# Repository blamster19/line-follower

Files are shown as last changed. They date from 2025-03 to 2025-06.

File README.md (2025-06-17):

# line-follower
Line follower for robot competition

## Introduction

This repository holds design and code of a line follower robot built for a racing competition which took place on 2025-06-11T17:00+0100 at the Faculty of Physics of University of Warsaw. The robot competed against five other machines and its score was based on the best time in three rounds. Machine built using contents of this repository won the first place with time 00:00:32,90. 
The team included:

* Jan Gers (captain)
* Tomasz Pniewski
* Magdalena Latała
* Maria Waligórska
* Wojciech Knop

Supervisor: Piotr Kaźmierczak

## Construction

### Hardware
1. **Chassis**  
	The chassis was 3D-printed with PLA on Prusa i3 MK3 from files: `./assets/chassis-model.stl`, `./assets/robot-motor-board.stl` and `./assets/robot-motor-shell.stl`. The motor shells were glued to the main body and motors put in them were later immobilized by boards.
2. **Electronics**  
	This is a list of parts used:
	
	|Part|Count|
	|---|---|
	|N20-BT03 micro 10:1 3000RPM - 12V|2|
	|KTIR0711S on 9x14 mm board with pins|7|
	|Solarbotics RW2i|2|
	|Pico Motor Driver HAT|1|
	|Raspberry Pi Pico H|1|
	|Step-down LM2596|1|
	|SparkFun BOB-13906|1|
	|9 V battery + clip|1|
	|Iduino ST1089|1|
	|Wires|a lot|
		
3. **Wiring**  
	Sensor output was connected through the multiplexer. Multiplexer control was connected to pins `27`,`12`,`13` and its output to analog pin `28`. IR sensor was connected to pin `26`. Motor control was done with pins `16`,`17`,`18`,`19`,`20`,`21` through dedicated ports on the driver HAT. The final construction was not utilizing the IR capability because of time reasons, but it should be functional or otherwise require a few tweaks. Step-down was connected to dedicated ports in the driver HAT and set to 8 V output for stability.
	
3. **Decorations**
	Because the team's name is 'Sigmas' we decided to glue small sigmas at the top of the motor shells. Since the track was getting dirty quickly, we wrapped a pipe cleaner around the sensor tray to act as a brush, which is both elegant and functional. To cover the wires we used synthetic pink feathers. We were quite happy with the avant-garde eclectic style of the robot.
	
### Software

The main loop is done with PD algorithm tweaked to the particular track. The program handles the exception of seeing no line (essential on a track with very sharp turns) by keeping memory of the last position of the line seen by the leftmost or rightmost sensor. Majority voting with this memory buffer decides on the direction of sharp turn which continues until any sensor sees black line again.

The code is hopefully well-documented and self-explanatory. The files which must be put in the Pico memory are `./code/main.py`, `./code/buffer.py`, `./code/motors.py`, `./code/pid.py` and `./code/sensors.py`. All alterations to the PD constants and motor speed shall be done inside `main.py`.

## The competition

This machine won with the best time 00:00:32,90. Below are some multimedia created during the event:

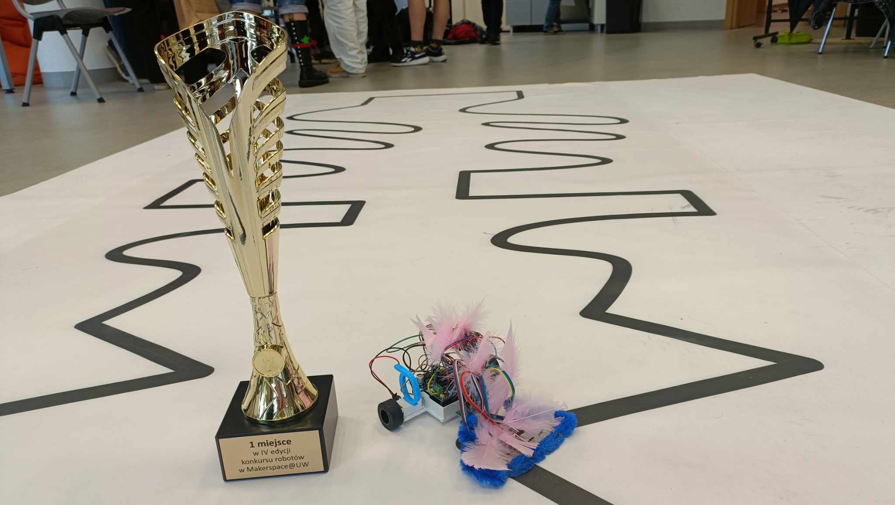
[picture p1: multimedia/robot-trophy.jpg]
Robot standing with the trophy


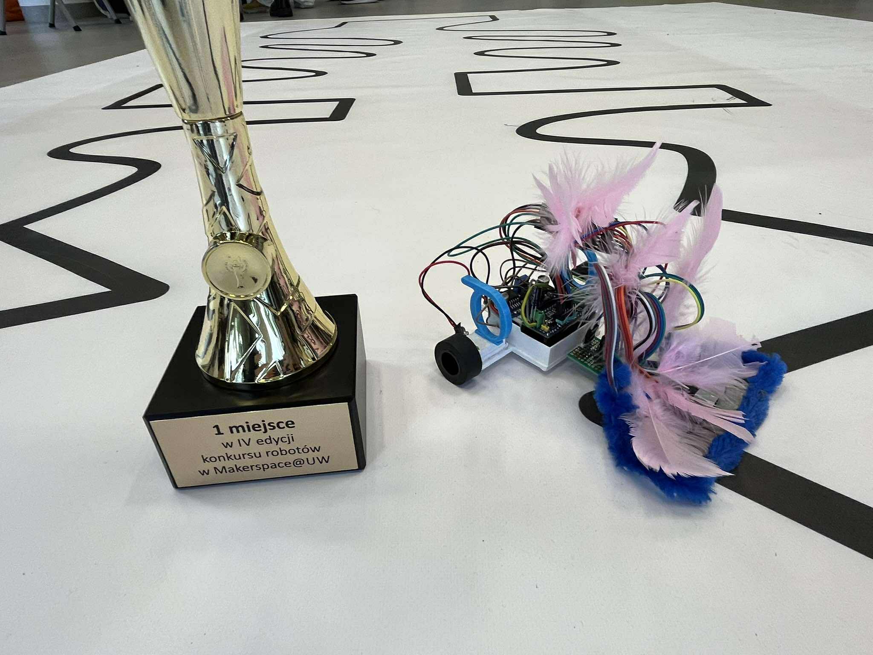
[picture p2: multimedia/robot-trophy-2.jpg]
Robot standing with the trophy closer


Robot following the line

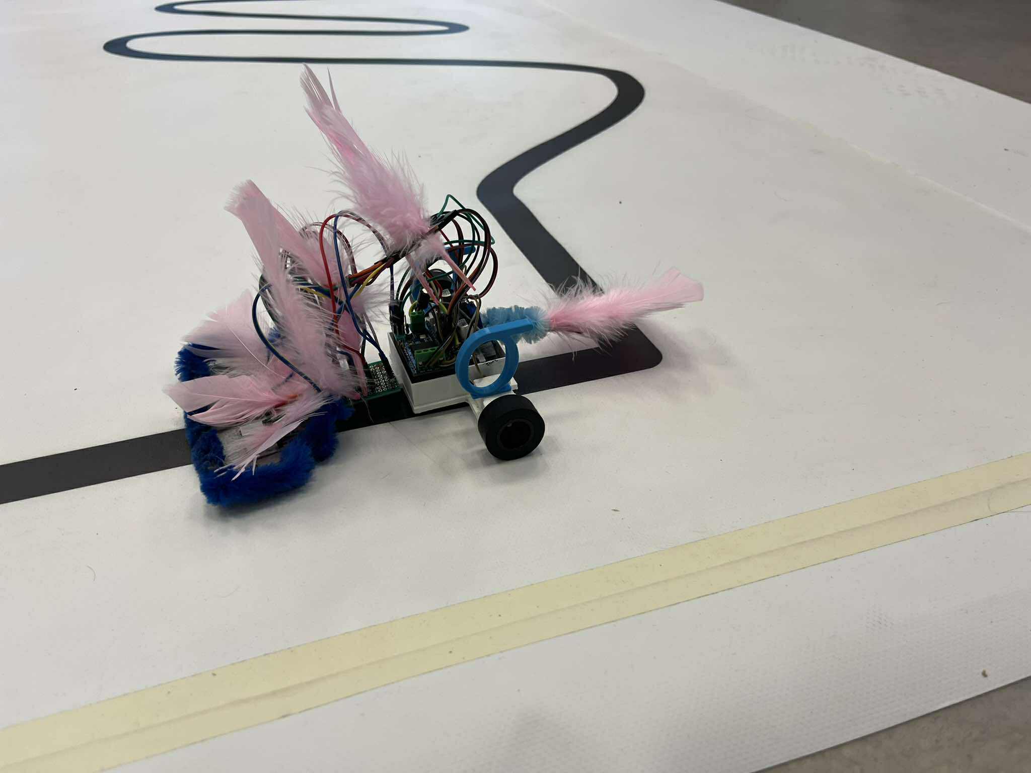
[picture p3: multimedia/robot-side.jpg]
Robot standing on track


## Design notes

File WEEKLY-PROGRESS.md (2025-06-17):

# Weekly progress

## 2025-02-24 -- 2025-03-02

* Arrival of parts: **ok**
* Repository initialization: **ok**
* First draft of chassis model: **ok**
* First print of chassis: **ok**
	* Needs to be better adjusted for printing, too much support needed
	* Relocation of PCBs and battery needed
* Sensor test: **ok**

## 2025-03-03 -- 2025-03-09

* Battery power test: **ok**
* Soldering of motor controller and step-down converter to RPi Pico: **ok**
* Driving test: **failed**
	* Motors pop out of the chassis under the load of battery
	* Motors do not move when weighted down with battery

## 2025-03-10 -- 2025-03-16

* Raising voltage: **failed**
	* Raspberry Pi Pico and potentially motor driver got fried
	* New parts ordered

## 2025-03-17 -- 2025-03-23

* Arrival of parts: **ok**
* Update of chassis model: **ok**
* Print of new chassis: **ok**

## 2025-03-24 -- 2025-03-30

* New motor driver: **ok**
* New power source: **ok**
* Drive test: **ok**
* Analog pin expander: **ok**
* Two-sensor reading: **ok**

## 2025-03-31 -- 2025-04-06

* Sensor calibration preliminary steps

## 2025-04-07 -- 2025-04-13

* Sensor calibration: **partial**
* Sensor code cleanup: **ok**
* Update of chassis model: **ok**
* New parts order: **ok**

## 2025-04-14 -- 2025-04-20

* Print of new chassis: **ok**
* Soldering sensors: **ok**
* Code tweaks: **ok**
* Sharp turn management: **ok**

## 2025-04-21 -- ##2025-04-27

* Soldering sensors: **ok**
* Code tweaks: **ok**
* Fried pin expander: **failed**
	* Pin expander melted the duc tape and stopped working
	* Probably because of prolonged usage

## 2025-04-28 -- 2025-05-04

* May Long Weekend

## 2025-05-05 -- 2025-05-11

* Analog multiplexers ordered instead of expander

## 2025-05-12 -- 2025-05-18

* Multiplexer: **ok**
* Drive test: **ok**
* New sensor code: **ok**

## 2025-05-19 -- 2025-05-25

* Code tweaks: **ok**

## 2025-05-26 -- 2025-06-01

* Installation of voltage converter: **ok**
	* Battery voltage drops caused noticeable speed difference
* New sensor tray: **ok**
* Code tweaks: **ok**
* Installation of two additional sensors: **ok**
* Installation of pipe cleaner in front of sensors: **ok**
* Optical tuning: **ok**
* Robot traverses full path: **partial**

## 2025-06-02 -- 2025-06-08

* New sensor tray: **ok**
* Code tweaks: **ok**
* Robot traverses full path: **success**
* Optical tuning: **ok**

## 2025-06-09 -- 2025-06-15

* Competition finale

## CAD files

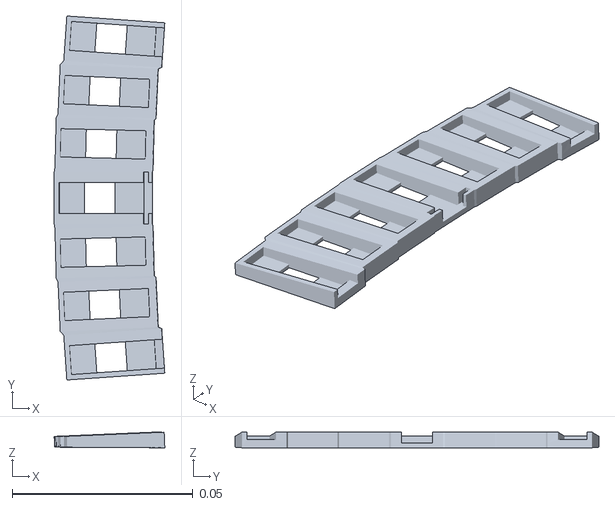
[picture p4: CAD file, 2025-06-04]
assets/sensors_hold.stl
0.0306 x 0.101 x 0.0043

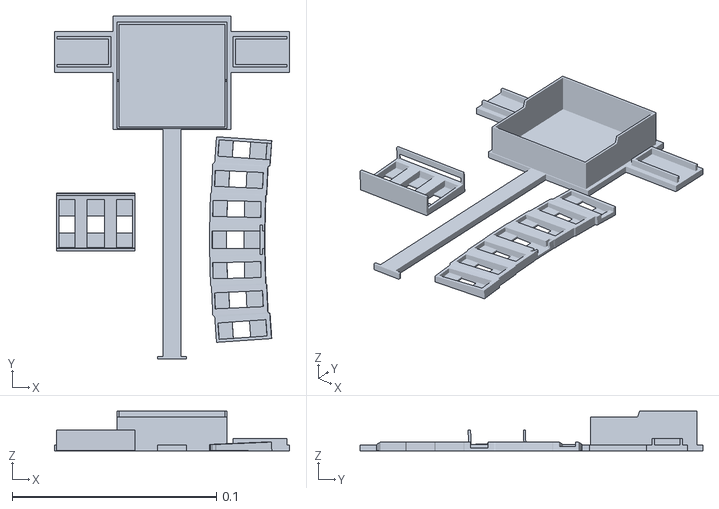
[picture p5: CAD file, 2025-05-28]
assets/chassis-model.stl
0.115 x 0.168 x 0.0195

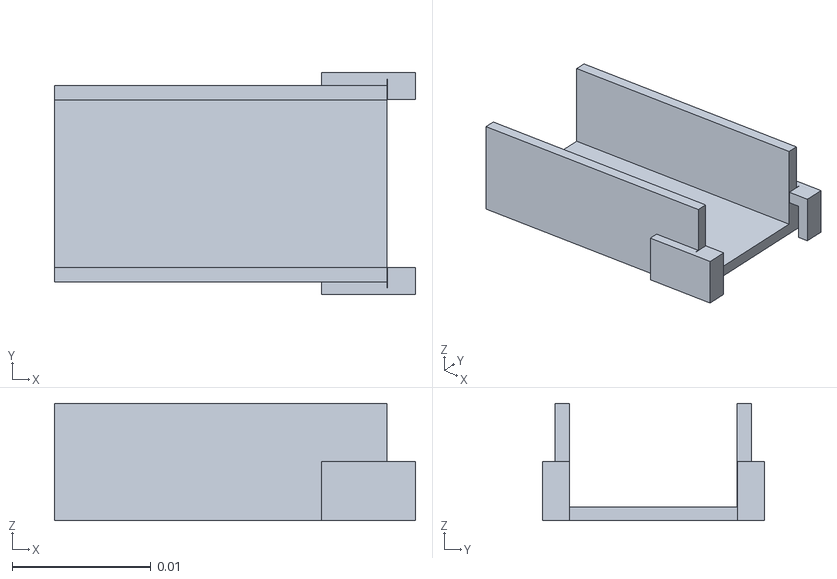
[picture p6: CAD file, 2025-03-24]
assets/robot-motor-shell.stl
0.0261 x 0.016 x 0.00848

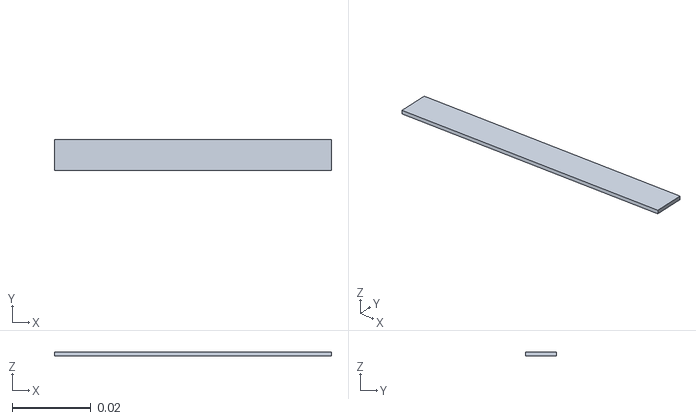
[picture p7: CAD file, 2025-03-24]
assets/robot-sensor-down-board.stl
0.0704 x 0.00781 x 0.000894

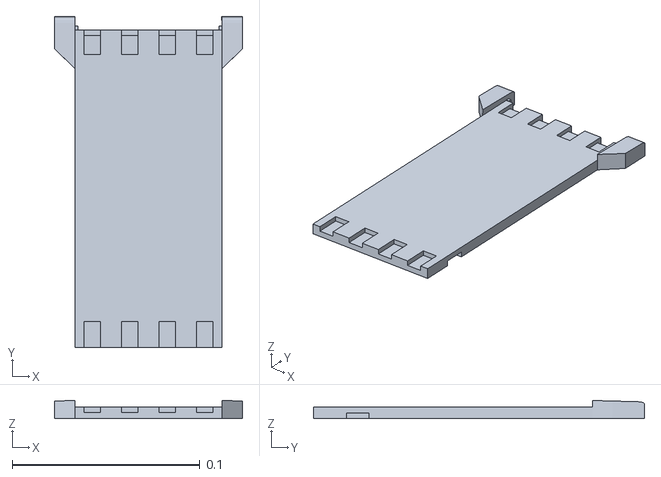
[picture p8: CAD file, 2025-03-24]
assets/robot-chassis.stl
0.1 x 0.176 x 0.00961

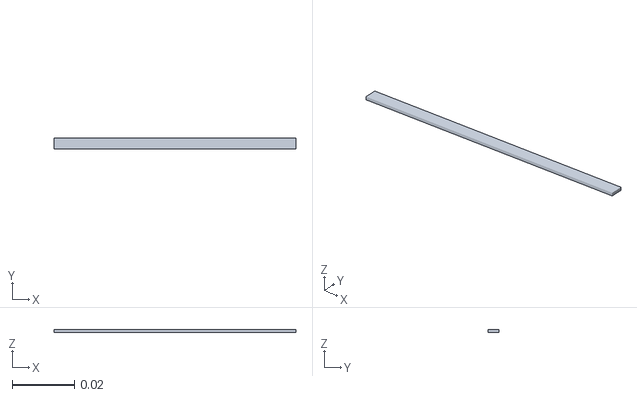
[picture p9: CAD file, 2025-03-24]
assets/robot-sensor-front-board.stl
0.0778 x 0.00355 x 0.000894

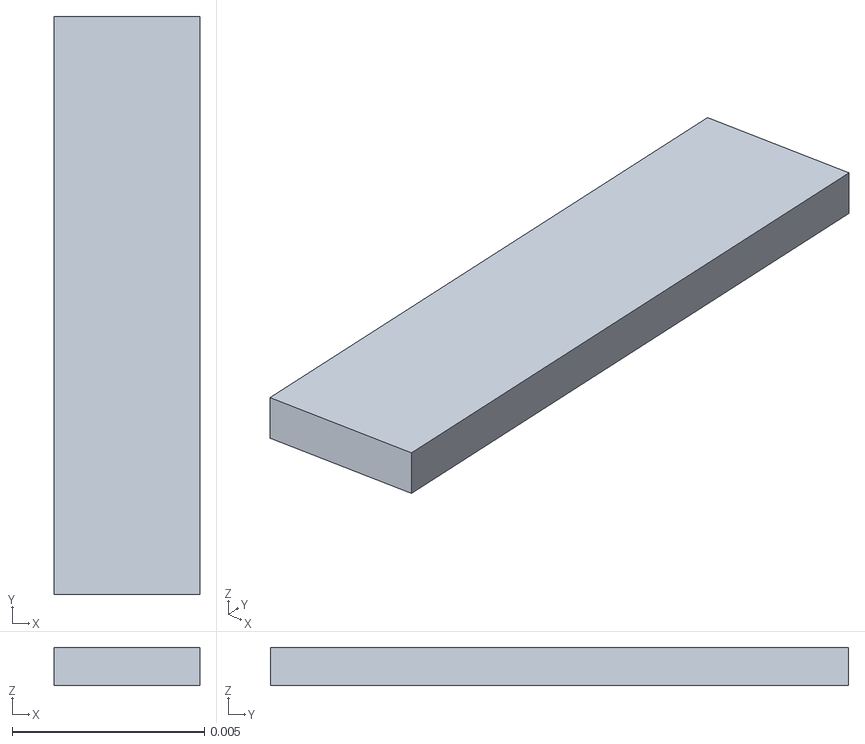
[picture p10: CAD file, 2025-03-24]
assets/robot-motor-board.stl
0.0038 x 0.0151 x 0.000991

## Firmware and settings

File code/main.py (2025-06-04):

from time import sleep
import time
from sensors import Sensors
from motors import Motors
from pid import PIDController
from buffer import CyclicBuffer
import _thread
from machine import Pin, time_pulse_us

DEBUG = False
# MODE = 'line pos'
MODE = 'sensor voltages'
# MODE='remote'

# Pins for the motors, multiplexer and remote control
motor_pins = {
    "left_forward": 21,
    "left_reverse": 20,
    "right_forward": 18,
    "right_reverse": 19
}
motor_enable_pins = [17, 16]

select_pins = (27, 12, 13)
adc_pin = 28 

rc_pin = 26

# Mapping of sensor position to multiplexer channel
# leftmost sensor is at 1.0 and rightmost is at 7.0
positions_to_mux_channel = {
    1.0: 5,
    2.0: 0,
    3.0: 1,
    4.0: 2,
    5.0: 3,
    6.0: 4,
    7.0: 6,
}

positions_to_mux_channel = [5, 0, 1, 2, 3, 4, 6]

# Sensor constants
THRESHOLD_MIN = 3.4      # Minimun voltage for sensor input thresholding
THRESHOLD_MAX = 5.0     # Maximum voltage for sensor input thresholding
EPSILON = 0.5           # Lower sensor inputs are considered to not be on the line
EPSILON_UPPER = 4.      # Higher sensor inputs are considered to be on the line
N_smoothing_memory = 2  # Length of memory buffer for sensor smoothing
smoothing_alpha = 0.99  # Alpha parameter for sensor smoothing
# border_mode = 'last'
border_mode = 'average'
N_direction_memory = 10

# Motor speed constants
K_se = 0.15              # Speed scaling for error values
K_sd = 0.15             # Speed scaling for derivative values
TIGHT_TURN_SPEED = 125.0 # The speed for tight turns
BASE_SPEED = 100.0         # The speed at which the robot moves when the line is perfectly aligned
PROPORTION = 1.5        # Proportion of wheel speeds for tight turns

# PID constants
middle_of_line = 4.0    # Point we consider to be the desired position
dt = 0.01               # Time step in seconds
Kp = -25.0               # Proportional gain
Kd = -0.4               # Derivative gain
Ki = -0.0              # Integral gain

battery_constant = 0.8
# 8.86 - 0.47
# 7.54 - 1.0


# Shared pulse signal and result
shared = {"new_pulse": False, "pulse_len": 0}
lock = _thread.allocate_lock()

def pulse_reader(rc_PIN, lock, shared):
    while True:
        # Read the pulse duration (blocking)
        pulse = time_pulse_us(rc_PIN, 1, 1000000)
        if pulse > 0:
            with lock:
                if shared["new_pulse"] == False:
                    shared["pulse_len"] = pulse
                    shared["new_pulse"] = True
        sleep(0.01)


def debug(mode, new_is_on, sensors):
    start_time = time.ticks_ms()           
    sensors.read_sensors()
    print(sensors.voltages)
    if mode=='line pos':
        print(sensors.get_current_line_position())    
        
    if mode=='sensor voltages':
        output = ''
        for sensor in range(7):
            output += 's'+str(int(sensor)) + '=' + str(sensors.voltages[sensor]) + ' '
        print(output)
    end_time = time.ticks_ms()
    elapsed_time_ms = time.ticks_diff(end_time, start_time)
    elapsed_time_s = elapsed_time_ms / 1000.0
    if elapsed_time_s < dt:
        # Sleep for the remaining time to maintain the loop frequency
        sleep_time = dt - elapsed_time_s
        sleep(sleep_time)
    if mode=='remote':
        rc_PIN = Pin(rc_pin, Pin.IN)
        if not rc_PIN.value():
            new_is_on = False if new_is_on else True
            sleep(0.3)
        print(new_is_on)
        return new_is_on
    return False


if __name__ == "__main__":

    # Initialize remote control
    rc_PIN = Pin(rc_pin, Pin.IN)
    #_thread.start_new_thread(pulse_reader, [rc_PIN, lock, shared])

    # Initialize motors, sensors
    motors = Motors(motor_pins, motor_enable_pins)
    motors.start()
    sensors = Sensors(positions_to_mux_channel, select_pins, adc_pin, threshold_min=THRESHOLD_MIN, memory_length=N_smoothing_memory, threshold_max=THRESHOLD_MAX, alpha=smoothing_alpha)

    # Initialize turn detection variables
    direction_buffer = CyclicBuffer(5)
    left_sensor_readings = CyclicBuffer(N_direction_memory)
    right_sensor_readings = CyclicBuffer(N_direction_memory)
    steps_line_right = 0       # Number of time steps since line was read by leftmost sensor
    steps_line_left = 0        # Number of time steps since line was read by rightmost sensor

    # Initialize PID controller
    pid_controller = PIDController(Kp, Kd, Ki, dt, setpoint=middle_of_line)

    # Robot state flags
    after_sharp_turn = False   # Tells if we just got out of a sharp turn
    stopped = False            # Tells if the motors are stopped  
    left = True                # Tells which direction we should turn if we lose the line next step
    is_on = False              # Tells if the robot is active (on/off from remote)
        
    try:
        if DEBUG:
            while True:
                is_on = debug(MODE, is_on, sensors)

        while True:
            with lock:
                if shared["new_pulse"]:
                    print("Pulse length:", shared["pulse_len"], "us")
                    if shared["pulse_len"] > 50000:
                        is_on = False if is_on else True
                    shared["pulse_len"] = 0
                    shared["new_pulse"] = False
            is_on = True
            if not is_on:
                if not stopped:
                    stopped = True
                    motors.stop()
                    # Reset the buffer after being turned off
                    direction_buffer = CyclicBuffer(N_direction_memory)
                sleep(dt)
                continue
            else:
                if stopped:
                    stopped = False
                    motors.start()

            # Measure start time for equal timesteps
            start_time = time.ticks_ms()

            sensor_voltages = sensors.read_sensors()
            position_weighted_average = sensors.get_current_line_position()

            control_output, error, derivative = pid_controller.update(position_weighted_average)
            speed = BASE_SPEED / (1 + K_se * abs(error) + K_sd * abs(derivative))
            
            # If all sensors do not see the line or all see the line, make a tight turn to get back on the line
            all_off_line = all(voltage < EPSILON for voltage in sensors.voltages)
            all_on_line  = all(voltage > EPSILON_UPPER for voltage in sensors.voltages)
            if all_off_line or all_on_line:
                # A neutral update to the PID controller and error buffer
                pid_controller.update(middle_of_line)
                direction_buffer.append(0.0)
                # Update flag that we were executing a sharp turn this time step
                after_sharp_turn = True
                motors.stop()
                motors.start()
                if left:
                    motors.tight_turn(-battery_constant * TIGHT_TURN_SPEED, PROPORTION)
                else:
                    motors.tight_turn(battery_constant * TIGHT_TURN_SPEED, PROPORTION)    
            else:

                # Stop the motors and try to stop spinning after ending the sharp turn
                if after_sharp_turn:
                    motors.stop()
                    after_sharp_turn = False
                    sleep(dt)
                    motors.start()
                    continue

                if border_mode == 'last':

                    if sensors.voltages[0] > EPSILON_UPPER:
                        steps_line_left = 0
                    else:
                        steps_line_left += 1

                    if sensors.voltages[6] > EPSILON_UPPER:
                        steps_line_right = 0
                    else:
                        steps_line_right += 1

                    if steps_line_left < steps_line_right:
                        left = True
                    else:
                        left = False

                if border_mode == 'average':

                    left_sensor_readings.append(max(sensors.voltages[0], 0.0))
                    right_sensor_readings.append(max(sensors.voltages[6], 0.0))
                    
                    print('l=' + str(left_sensor_readings.average() + 1.0) + ' r=' + str(right_sensor_readings.average() + 1.0)) 

                    if left_sensor_readings.average() > right_sensor_readings.average():
                        left = True
                    else:
                        left = False
                
                motors.set_direction(battery_constant * speed, battery_constant * control_output)
                direction_buffer.append(error)
            
            end_time = time.ticks_ms()
            elapsed_time_ms = time.ticks_diff(end_time, start_time)
            elapsed_time_s = elapsed_time_ms / 1000.0
            if elapsed_time_s < dt:
                # Sleep for the remaining time to maintain the loop frequency
                sleep_time = dt - elapsed_time_s
                sleep(sleep_time)
                
    except KeyboardInterrupt:
        pass
    finally:
        motors.stop()

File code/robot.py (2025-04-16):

from time import sleep
from pimoroni_i2c import PimoroniI2C
from breakout_ioexpander import BreakoutIOExpander
from array import array 
from machine import Pin, PWM

STOP = 0
RIGHTRIGHT = 1
RIGHT = 2
STRAIGHT = 3
LEFT = 4
LEFTLEFT = 5
NONE = 6

# Motor control pins
m1 = PWM(Pin(20))
m2 = PWM(Pin(21))
m3 = PWM(Pin(18))
m4 = PWM(Pin(19))

# Enable pins (if needed, set to output and enable)
en1 = Pin(17, Pin.OUT)
en2 = Pin(16, Pin.OUT)

# PWM frequency (adjust as needed)
PWM_FREQ = 1000  # Hz

m1.freq(PWM_FREQ)
m2.freq(PWM_FREQ)
m3.freq(PWM_FREQ)
m4.freq(PWM_FREQ)

def enable_motor():
    en1.value(1)  # motor 1 enable
    en2.value(1)  # motor 2 enable

def motor1_forward(speed):
    m1.duty_u16(int(speed * 655.35))  # 0-100% to 0-65535
    m2.duty_u16(0)

def motor1_reverse(speed):
    m1.duty_u16(0)
    m2.duty_u16(int(speed * 655.35))

def motor2_forward(speed):
    m3.duty_u16(int(speed * 655.35))
    m4.duty_u16(0)

def motor2_reverse(speed):
    m3.duty_u16(0)
    m4.duty_u16(int(speed * 655.35))

def motor_stop():
    for m in [m1, m2, m3, m4]:
        m.duty_u16(0)


def set_motors(direction):
    if direction == STRAIGHT:
        # all sensors on line - go straight
        motor1_forward(max_speed)
        motor2_forward(max_speed)
        #print('going straight')
    elif direction == LEFT:
        # left detection - gentle left turn
        motor1_forward(max_speed)
        motor2_forward(lesser_speed)
        #print('left turn')
    elif direction == RIGHT:
        # right detection - gentle right turn
        motor1_forward(lesser_speed)
        motor2_forward(max_speed)
        #print('right turn')
    elif direction == LEFTLEFT:
        # far left detection - sharp left turn
        motor1_forward(100)
        motor2_reverse(max_speed)
    elif direction == RIGHTRIGHT:
        # far right detection - sharp right turn
        motor1_reverse(max_speed)
        motor2_forward(100)
    elif direction == STOP:
        motor1_forward(0)
        motor2_forward(0)

THRESHOLD = 0.5

if __name__ == '__main__':
    # set pins

    PINS_BREAKOUT_GARDEN = {"sda": 12, "scl": 13}

    sensor_thresholds = {1: 0.5, 2: 2, 3: 0.5, 4: 0.5, 5: 0.5}
    sensor_positions = {1: "rightright", 2: "right", 3: "center", 4: "left", 5: "leftleft"}
    positions_sensors = {value: key for key, value in sensor_positions.items()}
    sensor_pins = {1: 10, 2: 7, 3: 9, 4: 11, 5: 13}
    ioe_adc_pins = sensor_pins.values()

    i2c = PimoroniI2C(**PINS_BREAKOUT_GARDEN)
    ioe = BreakoutIOExpander(i2c, address=0x18)

    for ioe_adc_pin in ioe_adc_pins:
        ioe.set_mode(ioe_adc_pin, BreakoutIOExpander.PIN_ADC)

    # initialize motor control
    enable_motor()
    
    max_speed = 50
    lesser_speed = 30

    memory_length = 50
    last_not_none = 0
    while True:
        # read sensors
        sensor_voltages = {}
        for sensor in sensor_pins.keys():
            sensor_voltages[sensor] = ioe.input_as_voltage(sensor_pins[sensor])
        
        voltage_left = sensor_voltages[positions_sensors["left"]]
        is_on_line_left = voltage_left > sensor_thresholds[positions_sensors["left"]]
        voltage_right = sensor_voltages[positions_sensors["right"]]
        is_on_line_right = voltage_right > sensor_thresholds[positions_sensors["right"]]
        voltage_center = sensor_voltages[positions_sensors["center"]]
        voltage_leftleft = sensor_voltages[positions_sensors["leftleft"]]
        voltage_rightright = sensor_voltages[positions_sensors["rightright"]]
        direction = STRAIGHT
        # P controller using all four sensors
#         if (voltage_center > sensor_thresholds[positions_sensors["center"]]):
            # all sensors on line - go straight
#             direction = "straight"
            #print('going straight')
        if (voltage_left > sensor_thresholds[positions_sensors["left"]] and voltage_right > sensor_thresholds[positions_sensors["right"]]):
            direction = STRAIGHT
            last_not_none = 0
        elif voltage_left > sensor_thresholds[positions_sensors["left"]]:
#         if voltage_left > sensor_thresholds[positions_sensors["left"]]:
            # left detection - gentle left turn
            direction = LEFT
            last_not_none = 0
            #print('left turn')
        elif voltage_right > sensor_thresholds[positions_sensors["right"]]:
            # right detection - gentle right turn
            direction = RIGHT
            last_not_none = 0
            #print('right turn')
        elif voltage_leftleft > sensor_thresholds[positions_sensors["leftleft"]]:
            # far left detection - sharp left turn
            direction = LEFTLEFT
            last_not_none = 0
        elif voltage_rightright > sensor_thresholds[positions_sensors["rightright"]]:
            # far right detection - sharp right turn
            direction = RIGHTRIGHT
            last_not_none = 0
        elif last_not_none >= memory_length:
            # no line detected - stop
            direction = STOP
            #print('not on line')
        set_motors(direction)

        print("leftleft=" + str(voltage_leftleft) + " left=" + str(voltage_left) + " center=" + str(voltage_center) + " right=" + str(voltage_right) + " rightright=" + str(voltage_rightright))
#         print(direction)
        sleep(0.02)

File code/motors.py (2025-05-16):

from machine import Pin, PWM

# motor wires connection: left then right; black, beige, black, beige

class Motors:
    def __init__(self, motor_pins, enable_pins, pwm_freq=1000):
        """
        Initializes the motors with the given pins and frequency.
        * motor_pins: A dictionary mapping motor names to their corresponding pins.
        * enable_pins: A list of enable pins for each motor.
        * pwm_freq: The PWM frequency for the motors.
        """
        self.motors = {name: PWM(Pin(pin)) for name, pin in motor_pins.items()}
        self.enable_pins = [Pin(pin, Pin.OUT) for pin in enable_pins] if enable_pins else None
        self.pwm_freq = pwm_freq

        for motor in self.motors.values():
            motor.freq(self.pwm_freq)

    def set_direction(self, base_speed, direction):
        
        right_motor_speed = max(min(base_speed - direction, 100.0), -100.0)
        left_motor_speed = max(min(base_speed + direction, 100.0), -100.0)

        if (right_motor_speed > 0):
            self.motors["right_forward"].duty_u16(int(right_motor_speed * 655.35))
            self.motors["right_reverse"].duty_u16(0)
        else:
            self.motors["right_forward"].duty_u16(0)
            self.motors["right_reverse"].duty_u16(int(-right_motor_speed * 655.35))

        if (left_motor_speed > 0):
            self.motors["left_forward"].duty_u16(int(left_motor_speed * 655.35))
            self.motors["left_reverse"].duty_u16(0)
        else:
            self.motors["left_forward"].duty_u16(0)
            self.motors["left_reverse"].duty_u16(int(-left_motor_speed * 655.35))
            
    def tight_turn(self, direction, proportion):
        
        if direction >= 0.0:
            left_motor_speed = (direction / proportion)
            right_motor_speed = -direction
        else:
            left_motor_speed = direction
            right_motor_speed = -direction / proportion
            
        if (right_motor_speed > 0):
            self.motors["right_forward"].duty_u16(int(right_motor_speed * 655.35))
            self.motors["right_reverse"].duty_u16(0)
        else:
            self.motors["right_forward"].duty_u16(0)
            self.motors["right_reverse"].duty_u16(int(-right_motor_speed * 655.35))

        if (left_motor_speed > 0):
            self.motors["left_forward"].duty_u16(int(left_motor_speed * 655.35))
            self.motors["left_reverse"].duty_u16(0)
        else:
            self.motors["left_forward"].duty_u16(0)
            self.motors["left_reverse"].duty_u16(int(-left_motor_speed * 655.35))
            

    def stop(self):
        for motor in self.motors.values():
            motor.duty_u16(0)
        if self.enable_pins:
            for enable_pin in self.enable_pins:
                enable_pin.value(0)

    def start(self):
        if self.enable_pins:
            for enable_pin in self.enable_pins:
                enable_pin.value(1)

        

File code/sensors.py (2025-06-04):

from machine import ADC, Pin
import utime

class Sensors:
    """
    Analog sensor readings, storing and smoothing of readings.
    Conventions: 
        - both raw and smoothed readings are rescaled to the 0-5 range;
        - voltages are stored in lists, order of voltages is order of sensors from left to right.

    Attributes:
        positions_to_mux_channel (dict): Maps sensor positions to MUX channels.
        select_lines (list[Pin]): GPIO pins used to select MUX channel.
        adc (ADC): ADC object for reading sensor values.
        alpha (float): Smoothing factor for averaging over past readings.
        memory_length (int): Number of past readings used in smoothing.
        threshold_min (float): Voltages below this are treated as no line.
        threshold max (float): Voltages above this are treated as line fully detected.
        prev_voltages (list[list[float]]): History buffer of raw voltage readings.
        smoothed_prev_sensor_values (list[float]): Truncated and averaged voltages from the history buffer.
    """


    def __init__(self, mux_channels, select_pins, adc_pin, alpha=0.9, memory_length=5, threshold_min = 0.8, threshold_max=3.4):
        """
        Initializes the sensors using an analog multiplexer.
        * positions_to_mux_channel: Mapping of position float -> mux channel (0-7)
        * select_pins: GPIO pins connected to S0, S1, S2 of the mux
        * adc_pin: ADC pin connected to the multiplexer output (e.g., ADC0)
        * alpha: smoothing factor
        * memory_length: number of previous sensor readings to store in memory
        * threshold_min: voltages below this are treated as no line detected
        * threshold max: voltages above this are treated as line fully detected
        """
        self.mux_channels = mux_channels
        self.alpha = alpha
        self.memory_length = memory_length
        self.threshold_min = threshold_min
        self.threshold_max = threshold_max

        self.select_lines = [Pin(pin, Pin.OUT) for pin in select_pins]

        self.adc = ADC(Pin(adc_pin))

        self.voltages = [0.0] * 7  # Initialize voltages for each sensor position
        
    def select_channel(self, channel):
        """
        Sets the multiplexer select lines to select the given channel (0-7)
        """
        for i, pin in enumerate(self.select_lines):
            pin.value((channel >> i) & 1) 

    def read_sensors(self):
        """
        Reads all sensors via the multiplexer.
        Returns a list of smoothed voltages.
        """

        # read voltages

        for i, channel in enumerate(self.mux_channels):
            self.select_channel(channel)
            utime.sleep_us(250)
            raw_adc = self.adc.read_u16()  # 16-bit ADC read
            voltage = (raw_adc / 65535.0) * 5  # Convert to voltage assuming 5V reference
            self.voltages[i] = voltage  # Store the voltage in the correct position

        # calculate and update the average of past readings
        self.get_truncated_and_smoothed_voltages()

        return self.voltages
       
    def get_position_weighted_average(self):
        """
        Calculates the voltage weighted average of the sensor positions.
        Since the line is seen for high voltages, the average is calculated
        using the sensor voltages as the weights of their positions.
        * sensor_voltages: A dictionary of sensor voltages or a list of sensor voltages
        * voltages_in_list: you know what that is
        """
        total_weight = 0.0
        weighted_sum = 0.0
                
        for i, voltage in enumerate(self.voltages):
            total_weight += voltage

            weighted_sum += float(i + 1) * voltage

        return weighted_sum / total_weight if total_weight != 0 else 0
    
    def truncate(self, voltage):
        """
        Clips voltage value between self.threshold_min and self.threshold_max.
        Rescales the values to the 0-5 range.
        """
        val = min(self.threshold_max, voltage) if voltage > self.threshold_min else self.threshold_min
        
        val_01 = (val-self.threshold_min) / (self.threshold_max-self.threshold_min) 
        
        return val_01*5
    
    def get_truncated_and_smoothed_voltages(self):
        """
        Uses last n=self.memory_length sensor readings to calculate
        smoothed voltage value for each sensor. Before smoothing, clips
        voltage values between self.threshold_min and self.threshold_max.
        """
        
        for i in range(len(self.voltages)):
            self.voltages[i] = self.truncate(self.voltages[i])


    def get_current_line_position(self):
        """
        Calculates position of the line as average of sensor positions
        weighted by their smoothed n=self.memory_length last readings.
        Updates the value of self.smoothed_prev_sensor_values.
        """
        return self.get_position_weighted_average()

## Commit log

2025-02-26 Add files for 3D printing
    [robot_chassis.stl]
2025-02-26 docs: update LICENSE document
    Attach the CC-BY-SA 4.0 license.
2025-02-26 chore: update directory structure
    [robot_chassis.stl]
2025-02-26 Fix small problems with the model
    [robot-chassis.stl, robot_chassis.stl]
2025-03-24 Updated 3D models
    Robot design was updated and split into a more modular format
    [robot-chassis.stl, robot-motor-board.stl, robot-motor-shell.stl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]
2025-04-16 feat: new chassis version
    [chassis-model.stl]
2025-05-13 refactor: IOExpander replaced by multiplexer
    [main.py, motors.py, sensors.py]
2025-05-14 refactor: add truncation and smoothing of voltage readings
2025-05-16 fix: working tight turns
    [main.py, pid.py]
2025-05-16 fix: adjust code to new sensor measurement
    [main.py, sensors.py]
2025-05-16 chnages voltages dict to voltages list
2025-05-20 fix: remote control and driving constants
    [main.py]
2025-05-21 Added a more robust remote control for powering off and on
2025-05-21 feat: made curvy sensor holder
    [sensors_hold.stl]
2025-05-21 Experimental tight turn control
    [main.py, pid.py, sensors.py]
2025-05-26 refactor: optimize `sensors` module
    Dynamic allocations and dictionaries were replaced with static lists.
    [sensors.py]
2025-05-28 feat: new chassis sensor tray
    New tray holds seven sensors and is slightly curved.
    [chassis-model.stl]
2025-05-28 Reorganized sensor mapping, improved voltage handling and PID
2025-05-28 Added support for 7 sensors
2025-06-04 feat: stable parameters and 7 sensors
2025-06-04 fix: update sensors
2025-06-04 fix: set final values of constants
    [main.py]
2025-06-04 fix: symmetric sensor tray model
    [sensors_hold.stl]
